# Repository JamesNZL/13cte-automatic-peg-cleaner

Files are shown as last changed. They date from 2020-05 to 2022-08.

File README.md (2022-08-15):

# Automatic Peg Cleaner

## Assessment Submissions

- [Brief Development `AS 91698`](./Documentation/Brief%20Development%20AS%2091698.pdf) (Achieved with Excellence)
- [Prototyping `AS 91611`](./Documentation/Prototyping%20AS%2091611.pdf) (Achieved with Excellence)
- [Electronics `AS 91904`](./Documentation/Electronics%20AS%2091904.pdf) (Achieved with Excellence)

## Issue

> Upon removal from the ground, my stakeholder’s tent pegs always have large amounts of soil and dirt stuck in between the three protruding beams.
> This is a common issue experienced with all tent pegs, but particularly Y stakes such as his, a Sea to Summit Ground Control Peg, but also similar products from other brands such as an MSR Groundhog.
> These pegs are very popular due to their high holding power and strength to weight ratio, with three beams to maximise the surface area of ground contact, and therefore the amount of friction.
> This also means that upon removal soil band dirt is likely to stick to the beams, particularly in softer ground with more moisture.

## Operating Principle

> Once a peg has been inserted through the hole in the top of the product, the laser tripwire is broken and the water jets automatically engage.
> Once the tripwire re-arms, the water jets disengage and the process repeats.
> If the laser tripwire is left intact for 3 minutes, the product will automatically turn itself off to conserve battery life.

## Conceptual Statement

> An intuitive, automated, eco-friendly solution to unreasonably dirty tent pegs of all shapes and sizes, this product easily cleans pegs to a brand new condition using high pressure water jets, automatically triggered by a laser tripwire.
> Economical in its water and energy consumption, all water used is also stored for recycling, and is easily used to water plants and flowers.

## Circuit Schematic

Circuit schematic

## PCB Design & 3D Render

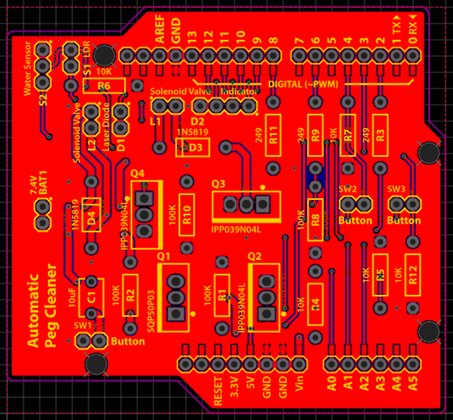
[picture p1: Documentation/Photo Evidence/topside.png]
PCB topside

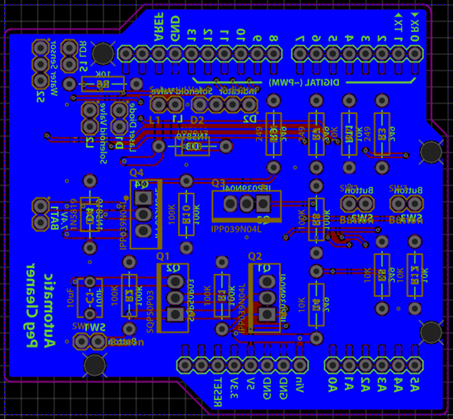
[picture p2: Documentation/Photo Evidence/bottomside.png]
PCB bottomside


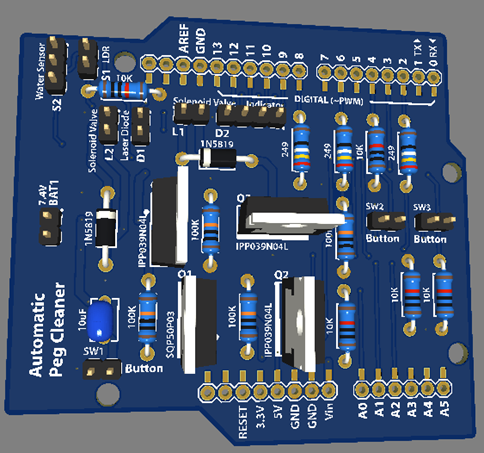
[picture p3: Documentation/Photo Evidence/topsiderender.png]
PCB topside render

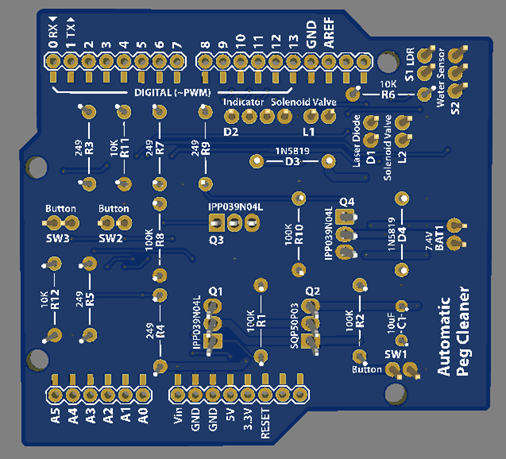
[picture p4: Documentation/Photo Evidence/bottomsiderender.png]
PCB bottomside render


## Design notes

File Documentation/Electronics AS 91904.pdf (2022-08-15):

jb16214 | Prototyping AS 91611 | 13CTE

# Electronics AS 91094

## Laser Tripwire

I started by hooking up an LDR to my Arduino and logging the analogRead() value, which returns the voltage between the output from the resistive divider created by the LDR and accompanying resistor
and ground. The circuit
at this stage looked like
as in Figure 1, with the
LDR in series with a 10k
resistor forming a
resistive voltage divider. To test this circuit, I ran the code as in Figure 2,
simply logging the
analogRead() from the
LDR pin.

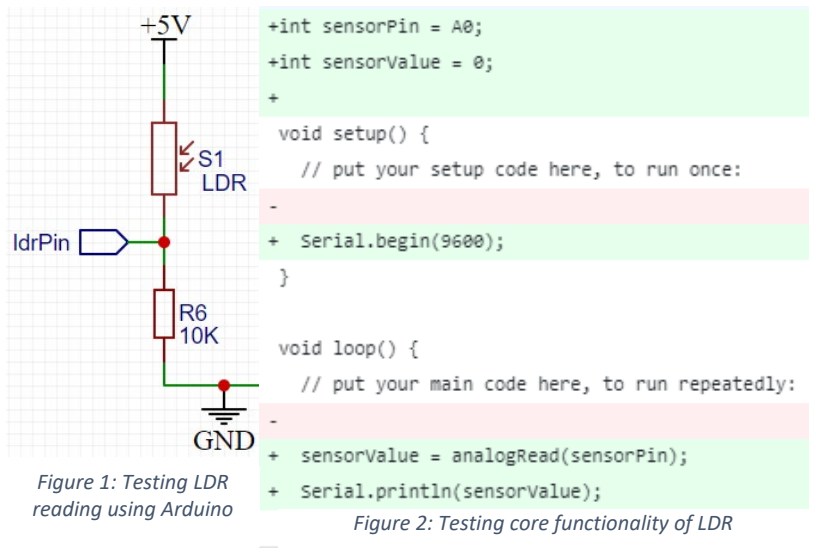
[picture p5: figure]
Figure 1: Testing LDR reading using Arduino

Once this behaved exactly as I was expecting, I added a trigger functionality to the code, with a variable defining a ‘trigger point’ where it would trigger if the light level was below triggerValue. I also made it so that the software would automatically calculate an appropriate light level to trigger at by reading the ambient light and finding the mid point between the ambient light level and the maximum possible reading, such that if the ambient light environment decreased it would trigger. By using this method in calculating the trigger point the code is far more versatile than if it were hard-coded in, as it could be moved from a brighter environment to a darker environment and still function as intended. This functions by trapping the code in a ‘while’ loop when the sensorValue is ‘safe’, only running the rest of the code when it falls below the trigger point. Although this is a bad solution for advanced programs as it is ‘blocking

Figure 2: Testing core functionality of LDR

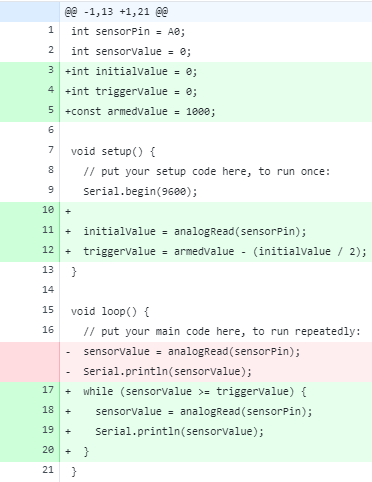
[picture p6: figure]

Figure 3: Implementing a trigger system code’, meaning no other code will run while the ‘while’ loop is still executing, it was sufficient for the proof-of-concept purposes I was using it for.
I ran into an issue with the code in Figure 3 as sensorValue was still set equal to 0 when it first ran the conditional statement of (sensorValue >= triggerValue), meaning it would immediately return false and therefore the while would never trigger. This meant that the tripwire would immediately trip, and the trigger system failed. To fix this, I initialised sensorValue = analogRead(sensorPin) before the while loop, to ensure it had a real value.

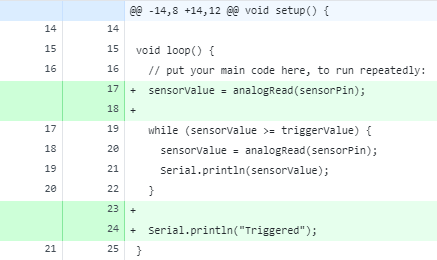
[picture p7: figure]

Figure 4: Bug fix for Figure 3
The next change I made was to improve the calculation for triggerValue, by increasing the data set used to calculate it by averaging out five values. This improves the accuracy of initialValue, and in turn results in a more accurate triggerValue.

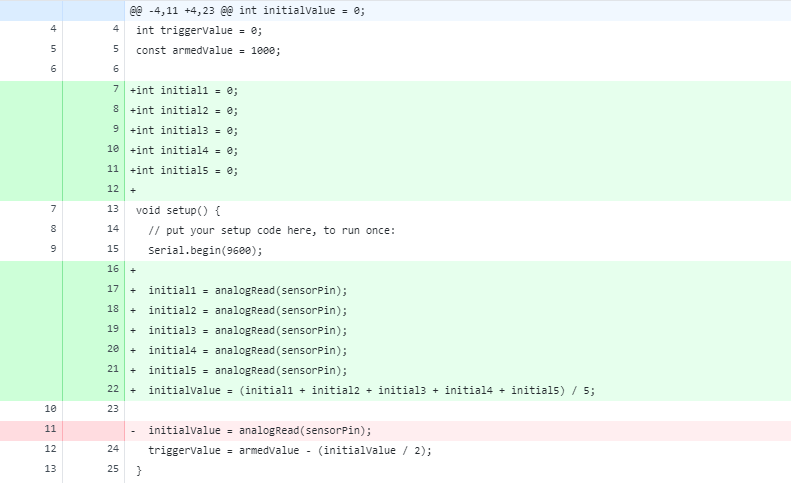
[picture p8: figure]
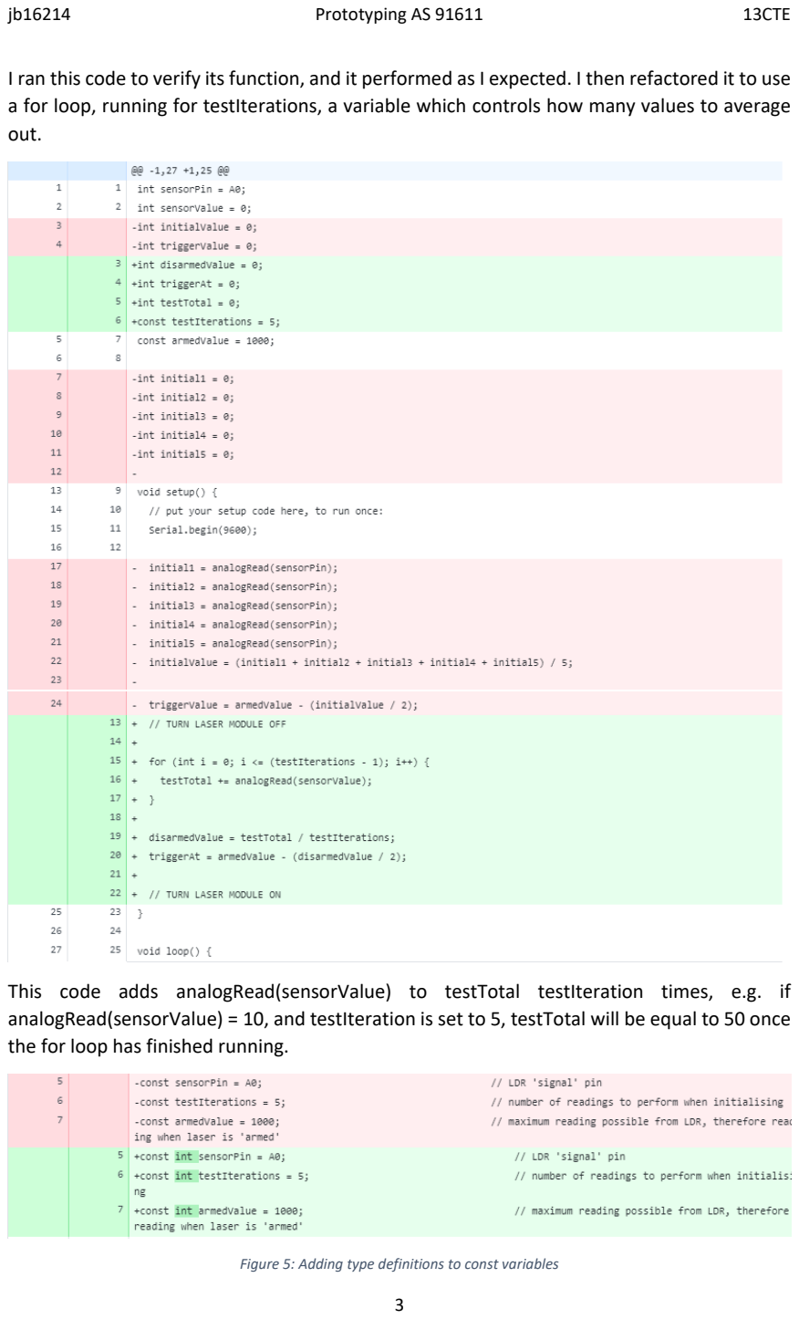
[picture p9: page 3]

I ran this code to verify its function, and it performed as I expected. I then refactored it to use a for loop, running for testIterations, a variable which controls how many values to average out.

This code adds analogRead(sensorValue) to testTotal testIteration times, e.g. if analogRead(sensorValue) = 10, and testIteration is set to 5, testTotal will be equal to 50 once the for loop has finished running.

Figure 5: Adding type definitions to const variables

## Laser Diode

Following some further minor optimisations to the LDR trigger code I then started on getting the laser to function, which I started with just setting up a Blink program with the laser connected to pin 13.

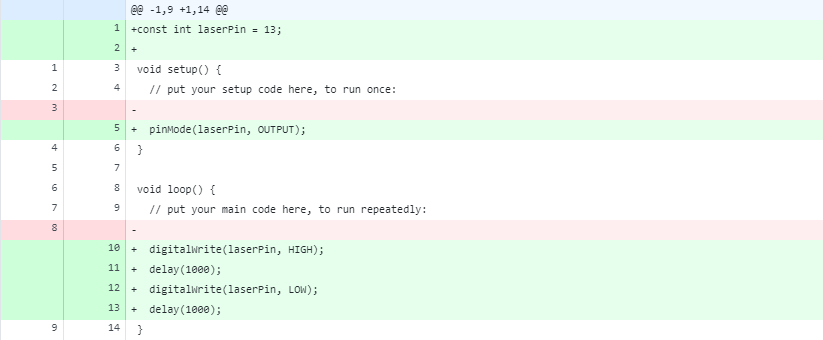
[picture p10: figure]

Once I verified through testing that the laser diode would behave exactly like a regular LED I then combined the two code files, adding the laser component of the tripwire system.

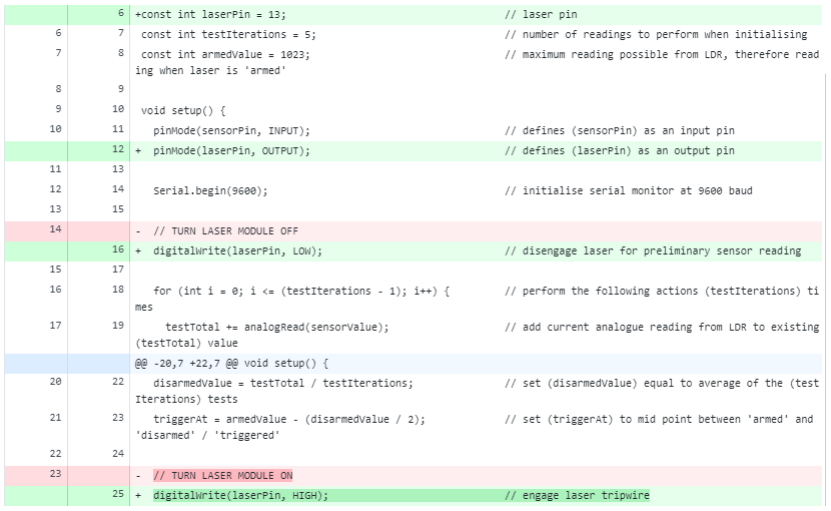
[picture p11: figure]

The first thing I did was to adjust the initialisation system to better represent the real trigger point, by ensuring the laser was turned off during the calculation. This means the real ambient value is taken, which can them be used to calculate an appropriate trigger value if the trigger value is broken and the laser is not in contact with the LDR. As the for loop is also ‘blocking code’, the laser will not be turned on until the readings have finished.

In order to test this code to ensure the calculation and tripwire is fully functioning, I added Serial.print lines to give debugging output, specifically logging the calculated value for triggerAt.

https://youtu.be/l-XJrVRsnDY - Testing laser tripwire

## RGB LED

Once I had my laser tripwire all testing and working, I then looked to add a red/green indicator to show whether everything was set up and good to go. To do this, I again created another proof-of-concept file, which I used to ensure the colour control would work as I was expecting it to.

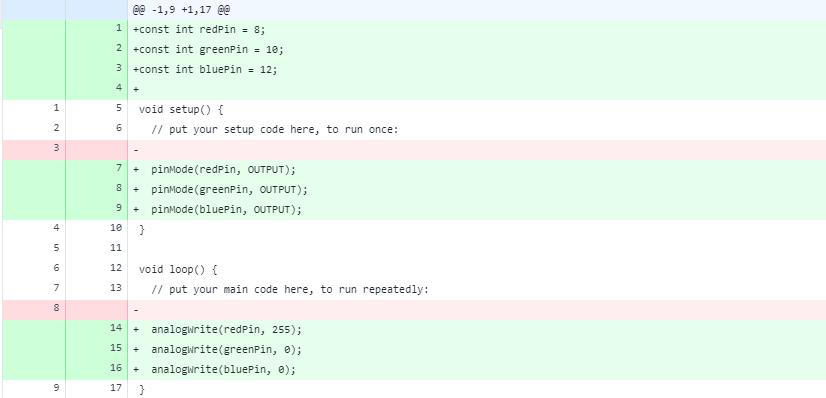
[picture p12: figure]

Once I ran and confirmed that this code functioned, I then decided to use digitalWrite() instead of analogWrite() for the RGB LEDs, as I did not need finer analog control, and I decided it would be easier to use a boolean set of 0/1 or LOW/HIGH instead of using 0 and 255.

I then implemented this RGB LED code into the main Laser Tripwire file, and configured it such that if the tripwire failed to initialise it would display red, or it would display green if everything were set up correctly.

https://youtu.be/d2IjNq5b3FE - Testing laser tripwire with RGB LED integration (LED is at bottom left of screen)

I then slightly refactored the laser tripwire code to do the ambient light level calculations before checking that the laser has turned on. This modifies the initialisation process from –
1. Turn laser on
2. Check laser is on
3. Turn laser off
4. Calculate ambient light level
5. Turn laser on
6. Check laser has turned on To –
1. Calculate ambient light level
2. Turn laser on
3. Check laser is on

I found that I had unexpected behaviour having the laser connected to pin 13 due to the Uno’s built in LED, and so I took the opportunity to re-map the pin assignments. I also used this chance to make sure the RGB LED pins were all next to each other, and so I decided to use pins 9, 10 and 11.

## Circuit Schematic

Once I had my proof of concept code files completed, I worked on developing the actual circuit for my project. To do this, I used EasyEDA to create my project schematic and later to produce the PCB design, the final results of which are shown below, with full development available alongside everything else in my GitHub repository: https://github.com/JamesNZL/13CTE, with development specific to the circuitry at: https://github.com/JamesNZL/13CTE/commits/master/Circuit/projects/Automatic%20Peg%20Cleaner. (https://github.com/JamesNZL/13CTE/commits/master/Circuit/projects/Automatic%20Peg%20Cleaner)
Commit history: https://github.com/JamesNZL/13CTE/commits/master

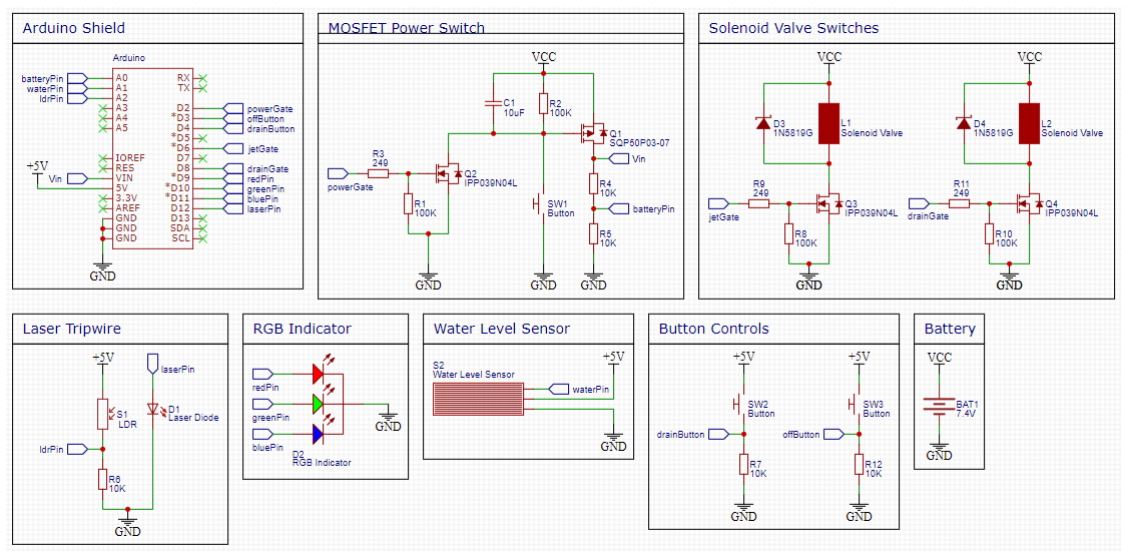
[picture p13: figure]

A notable design development choice I made was to add Schottky diodes D2 and D3 in reverse bias across the solenoid valves as flyback diodes, in order to prevent any unwanted voltage spikes and sparking due to the collapse of their magnetic fields.

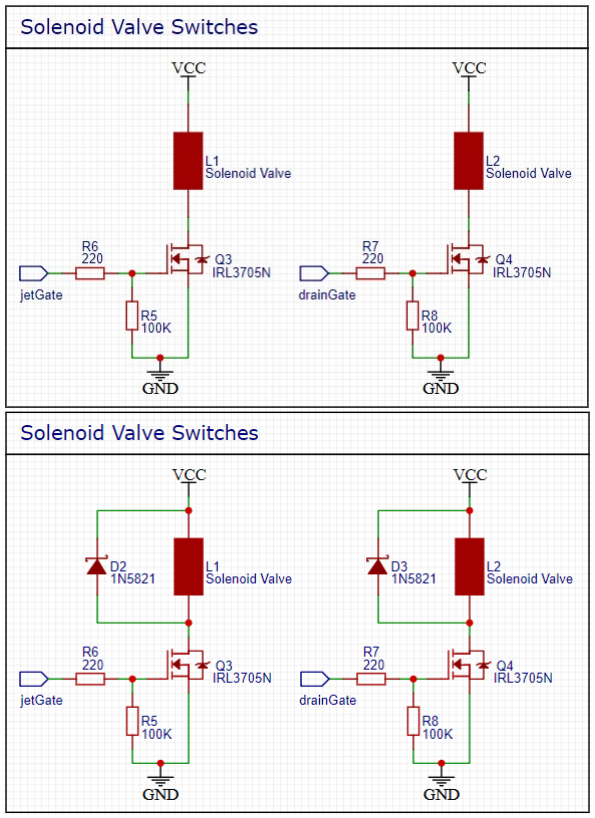
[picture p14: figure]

Another addition I made later on was the addition of a pair of voltage sense resistors R4 and R5 as shown in the image below, which form a resistive voltage divider allowing the Arduino to monitor the battery’s voltage. I used this to detect if the battery needed to be charged, notifying the user through blinking the indicator LED.

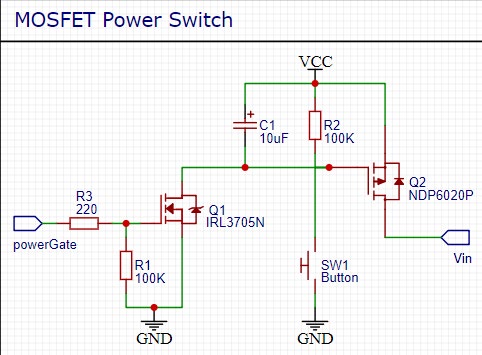
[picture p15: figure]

Figure 6: Without voltage sense resistors
Otherwise, my circuit schematic was reasonably straight-forward, with the only other circuit segment that was relatively advanced being the circuit for my MOSFET power switch, which I used to allow the Arduino to turn itself on when the user pushes the on button, and keeping itself on until the user pushes the off button.

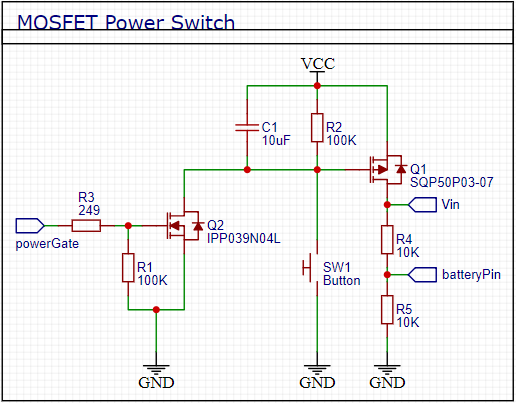
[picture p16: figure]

The way this circuit works is that the pair of P-Channel and N-Channel MOSFETs work together to switch the output of the circuit between GND and VCC, connected to the Arduino’s Vin pin, where the Arduino’s GND is permanently grounded. The circuit works as when the user pushes switch SW1 the gate of the P channel MOSFET Q1 is pulled to GND, connecting VCC at the drain to the Arduino’s Vin at the source. This means the Arduino begins to turn on, with a voltage output at batteryPin of half of the current voltage of the 7.4V nominal battery, which is used to check whether the battery needs to be recharged. SW1 can then be released as capacitor C1 will continue to keep the PMOS’s gate low, allowing the Arduino to fully boot. Once the Arduino has fully turned on, it outputs HIGH on the powerGate pin, keeping the NMOS Q2 switched in an ON state, which maintains the GND path for the gate of Q1. If the Arduino then needs to be turned off, it simply needs to switch powerGate LOW, which in turn switches Q1 off.

## Components Selection

I chose to use MOSFETs rather than NPN and PNP transistors for a variety of reasons, such as to minimise the current draw while switched on due to the tiny Rds(on) at 5V of just 0.0039 ohms and 0.007 ohms for my N and P MOS respectively. I found both using Digikey’s parametric search, from which the IPP039N04LGXKSA1 N-channel MOSFET and SQP50P03-07_GE3-ND P-channel MOSFET were the most appropriate for my needs and the most price effective in small quantities. Both MOSFETs are ‘logic level’, meaning they are designed for 3.3V or 5V logic circuits, with threshold voltages of gate-source (i.e. the voltage required to switch the MOSFET fully on) of 1.2V minimum and 2V maximum for the NMOS and -1.5V minimum and -2.5V maximum for the PMOS, easily manageable by my 7.4V battery / 5V Arduino.
I chose to place a gate resistor (R3) on my NMOS connected to the Arduino to ensure that the gate capacitance did not result in a high initial current draw greater than my Arduino can handle, therefore using Ohm’s law I used a maximum current draw of 20mA (half of the Arduino’s maximum of 40mA), which at 5V gives a resistance of 250 ohms, and so I chose a 249 ohm resistor. As MOSFETs are driven by voltage and not current (compared to a BJT transistor), there is no effect whatsoever on the speed or effectiveness of the FETs as switches. To calculate the power, I used PP = VV2
RR

with VV = 5 and RR = 250, giving me a

maximum instantaneous power draw of 0.1W. I decided to use a 1/4W resistor to give some buffer over the 0.0125W tolerance for a 1/8W resistor, with next-to-nil compromise in price or size.
I am also using gate pull down and pull up resistors (R1 and R2), to prevent floating states when the Arduino is turned off or when the switch and Arduino is off respectively for the N and P channel FETs, for which I chose 100K resistors to minimise the voltage loss over the resistive divider created by R1 and R3, and to minimise current draw to a miniscule 50 microamps, which is desirable for my battery-powered project.

To calculate the appropriate capacitance of C1 to sustain a reasonable boot time for the

# Arduino I used VV = VVss ⋅ ee

−tt
RRRR where V is equal to the threshold voltage of the FET’s gate, Vs is

the supply voltage (i.e. 7.4V), R is the resistor through which C is discharging, C being the capacitance value, and t being the time taken to discharge from Vs to V.
Rearranging for C, I got CC = −tt

# RRRRRR vv

vvss

# , into which I plugged in tt = 2, VV = −1, VVss = −7.4VV, RR = 100KK

to get C = 9.9926 E⁻⁶ Farads, or 10 microfarads.
By using 2 seconds I am ensuring that even with an extremely quick button press the Arduino will have enough time to fully turn on, which I am further ensuring by programming my Arduino using a second Arduino as ISP, meaning the Arduino does not need to run the bootloader and therefore is ready to go within milliseconds.
I did not require a current limiting resistor in series with my laser diode in order to protect my Arduino as it has an integrated 91 ohm resistor, which at its rated 5mW at 5V it will consume a maximum of 1mA, easily within the Arduino’s 40mA limit.
I determined an appropriate resistance to use in series with my LDR to create its voltage divider experimentally, using the following table:

I started by measuring the resistance of the LDR at varying light levels using a digital multimeter, and then using a 10k resistor and a 47k resistor and trying the results. I chose the values of 10k and 47k in an attempt to concentrate the accuracy of the LDR in the range where the ambient lighting will typically be, i.e. in an enclosed 3D printed product. Therefore, I chose 10k to create a 50/50 ratio at a dim light level and 47k to experiment tending towards a darker environment, as 47k was the closest value I had to 50k. Even accounting for the expected darker light levels of the final product, I found it was overwhelmingly more reliable to stick with a 10k resistor for maximum versatility, and therefore I did so.
For the armed tripwire, a maximum voltage of 4.943V translates to an analog reading of 1011, as 0.9889 (voltage divider ratio) * 1023 (maximum value) = 1011.

I decided it was not necessary to include reverse polarity protection in my circuitry, as I am using a keyed XT60 connector for my LiPo battery and a keyed MOLEX connector to connect my peg cleaner to the control box, therefore there is next to no risk of reverse polarity in normal operation.
To decide on a flyback diode for my solenoid valves I was looking for an average forward current of around 1A, to provide a decent buffer for the 500mA of current draw I expected from my solenoid valves. Using the DigiKey parametric search, I found the 1N5819, which has up to 25A of surge current and up to 40V of reverse voltage, meaning it was more than adequate for my application.

## PCB Development

My initial plan to produce and fabricate my PCB was to use our previous Voltera prototyping machine to validate that the circuit was fully functional on a proper board and not just on the breadboard, after which I would have it fabricated by a prototyping company such as JLCPCB. Multiple aspects of the plan changed however, and I ended up not having the time to realistically send my completed PCB design off and wait for it to arrive, and also we moved away from the Voltera printed ink circuit boards back to a CNC miller. Therefore, my final PCB being used in my project was produced using the school’s CNC miller.
Various different versions of my PCB design:

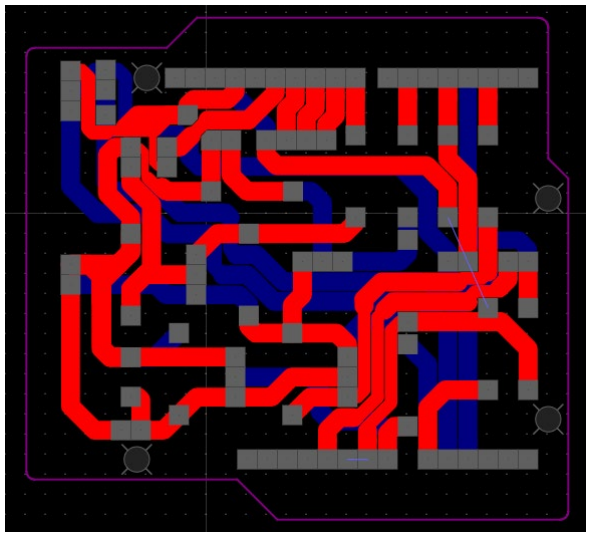
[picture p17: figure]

Figure 7: Top layer of my EasyEDA PCB design for the miller

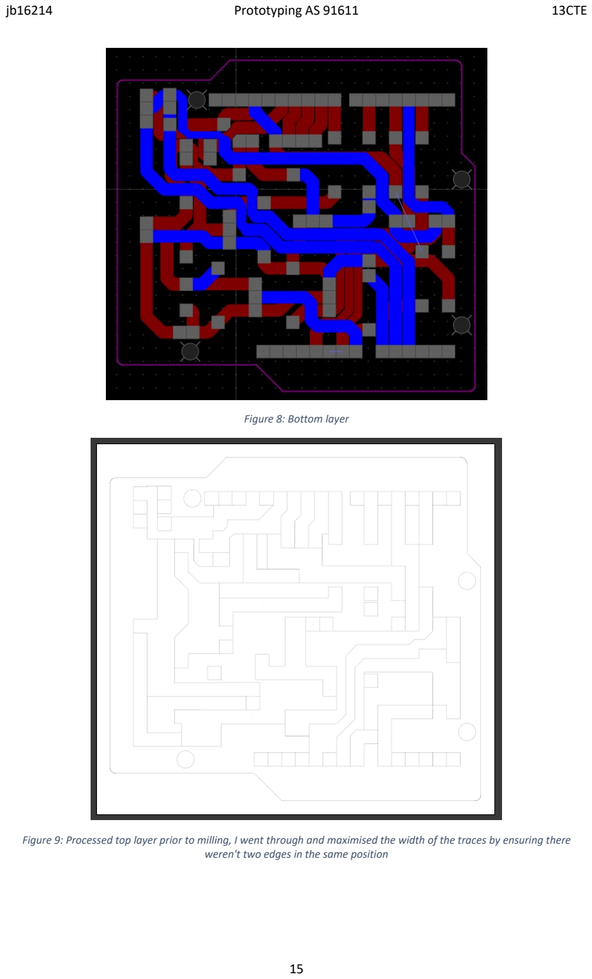
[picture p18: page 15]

Figure 8: Bottom layer

Figure 9: Processed top layer prior to milling, I went through and maximised the width of the traces by ensuring there weren't two edges in the same position

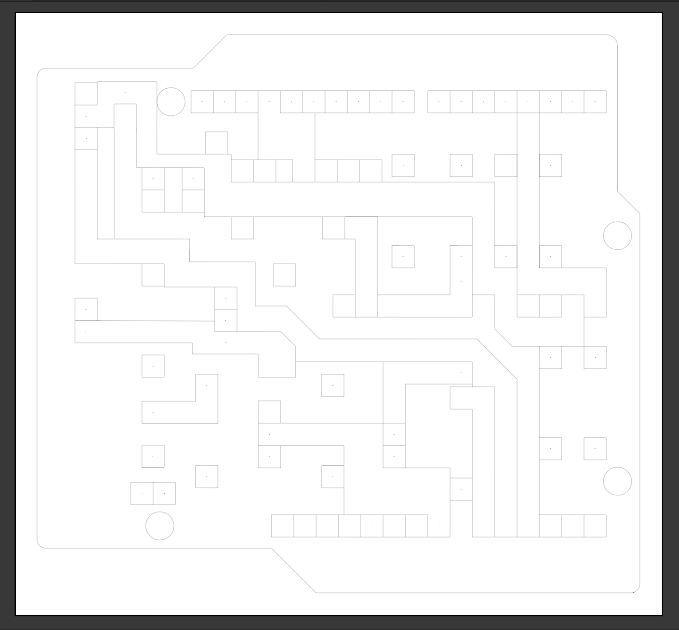
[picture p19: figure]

Figure 10: Processed bottom layer

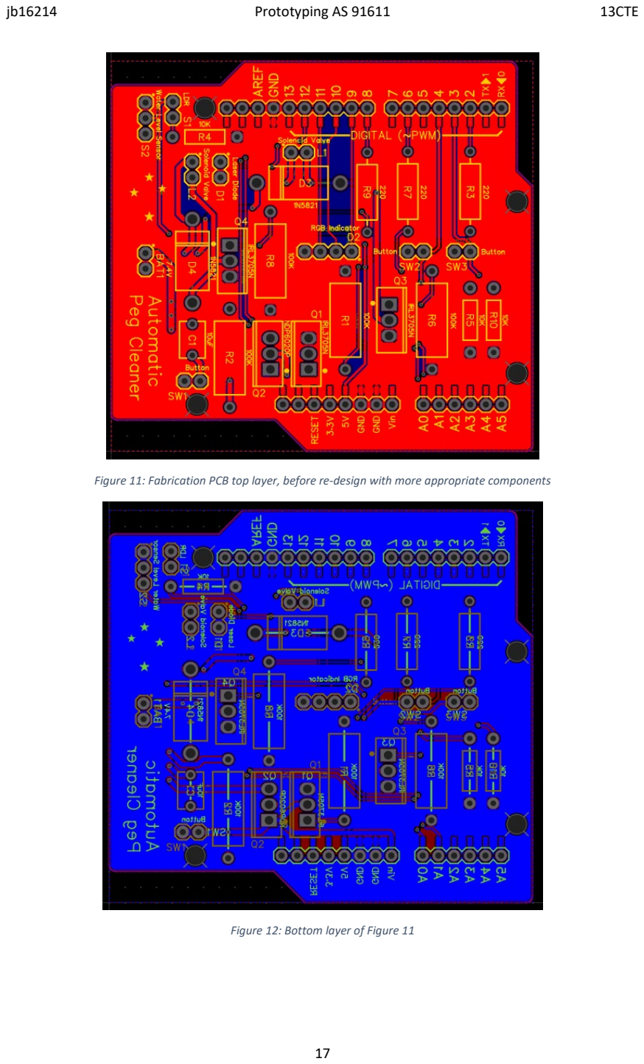
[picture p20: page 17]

Figure 11: Fabrication PCB top layer, before re-design with more appropriate components

Figure 12: Bottom layer of Figure 11

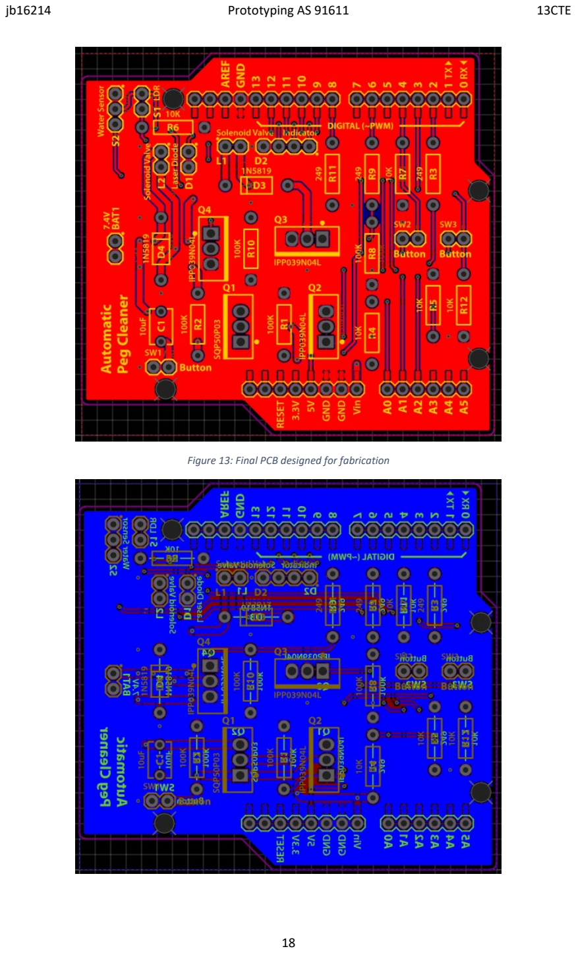
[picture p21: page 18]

Figure 13: Final PCB designed for fabrication

For my early versions such as the one I designed for the Voltera, my only goal was to ensure good quality electrical connections between A and B, in order to verify the performance and functionality of the circuit. Once I achieved that, I then went back and continued to iterate and improve, using design best practises such as using a GND plane/copper fill on my boards, enforcing a convention of North-South and East-West on my top/bottom layers to avoid routing conflicts, using vias to tidy up board layouts, and using GND stitching vias. By aiming to have my designs fabricated professionally, I was able to incorporate these elements into my designs as I could be confident that they would be able to be produced within the capabilities of the machines, unlike if I were to make them myself.
As we eventually moved away from using the Voltera at school, it meant the capabilities and restrictions I had to prototype my board at school changed drastically, as the CNC miller offered some significant advantages but also some disadvantages over the Voltera. The miller is far more robust and easier to operate than the Voltera, resulting in a board that is easier to debug and test, as well as to solder to. However, the design process to actually fabricate the board became far more complex, where while the Voltera simply needed the exported Gerber files directly from the PCB design software, the CamCut CNC required a proprietary and non-standardised .FAB fabrication file. This meant I had to export my designs from EasyEDA as a PDF rather than as a set of Gerber files, such that I could end up with a file readable by 2D Design. The only way we knew to get a workable .FAB file for the CNC miller was to export from 2D Design using a pre-loaded export engine and then run an executable on one of the school’s computers, and so I kept jumping through applications and file formats until I found one that resulted in a workable work-around. Eventually, I found I needed to export as a PDF and use Adobe Illustrator to convert it to a .DWG file readable by AutoCAD, which could then export as a .PLOT file that was recognisable by 2D design. We could then export using the CamCut PLOT settings, and putting that through the convert.exe, we ended up with a file that could be milled.
This meant it was somewhat more difficult to quickly prototype iterations of my PCB and especially if I wanted to use Illustrator to process my exported EasyEDA pdf so that the lines were as efficient as possible, however in the end resulted in a functional and working PCB.

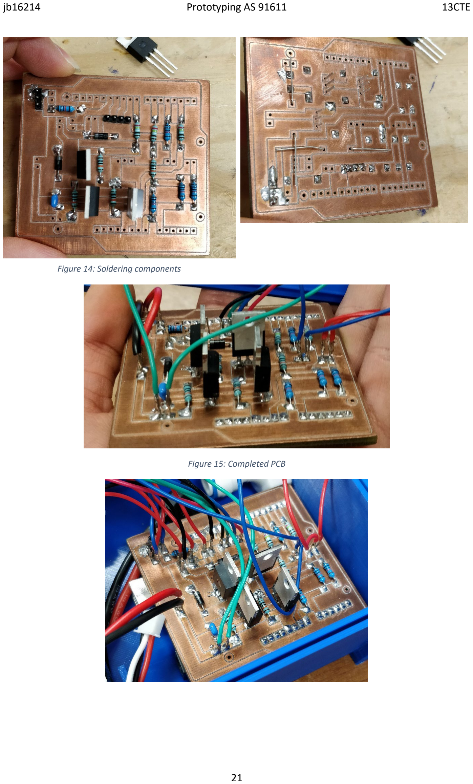
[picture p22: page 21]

Figure 15: Completed PCB

Figure 14: Soldering components

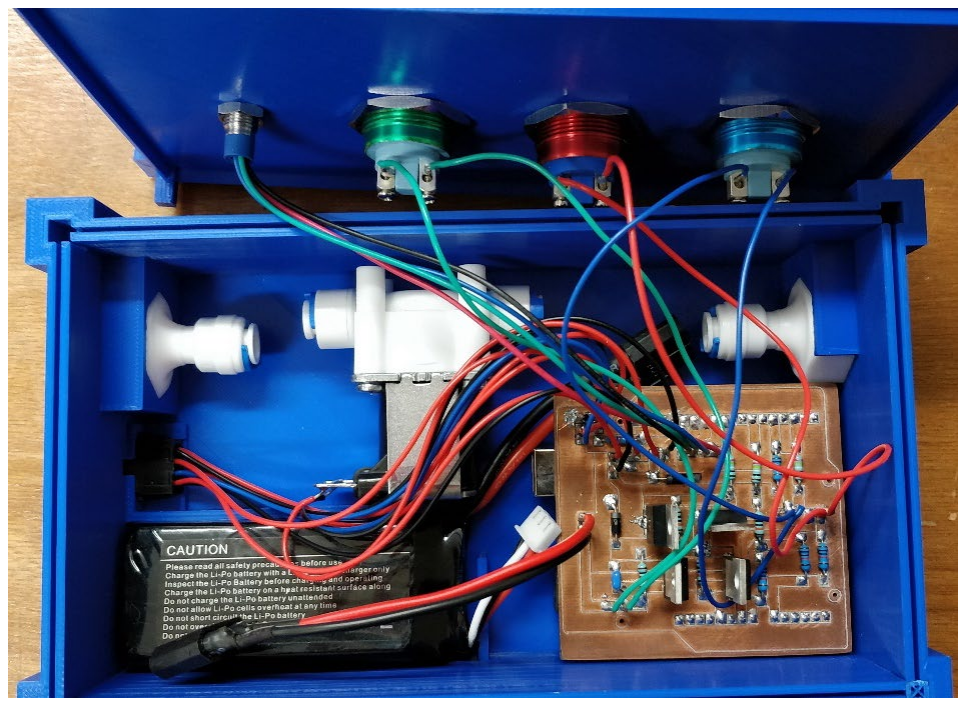
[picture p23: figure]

Figure 16: Completed PCB in enclosure

## Arduino as ISP

To program my Arduino, I used a second Arduino as a Programmer and used the ArduinoAsISP functionality to program the one I was using in my project. By using this method, I am ensuring the Arduino bootloader is not loaded on to my target Arduino, as therefore does not execute the bootloader processes when it first starts up. This consequently means that on start-up it immediately begins running my project code, and therefore will switch the pin connected to the MOSFET on extremely quickly. I decided to use this method of programming my target Arduino instead of the usual direct upload as by using the conventional upload, the IDE will automatically also upload Arduino’s bootloader to the target alongside the project code, which runs on start-up. What the bootloader does is check if the Arduino is trying to be programmed, and if so establishesthe connection in order to accept the incoming code. Although this only takes roughly a second to fully complete and to move on to the actual project code, I needed the target to turn on as

quickly as possible in order to ensure the capacitor did not discharge below the threshold needed to have the Arduino turn on, in the event that the user only gave the button a short tap.
Arduino as ISP uploads the program code from the programmer to the target using the SPI interface/protocol, or Serial Peripheral Interface. SPI is a synchronous interface, meaning that there is a clock signal controlled by the master device, i.e. the programmer, and used by the

Figure 17: From
https://www.arduino.cc/en/Tutorial/BuiltInExamples/ArduinoISP (https://www.arduino.cc/en/Tutorial/BuiltInExamples/ArduinoISP)

slave device(s), i.e. the target. SPI uses four pins as shown in the diagram above (not including the +5V and GND connections), by convention called SCLK, MOSI, MISO and SS.
SCLK | Serial clock | Controlled/output by the master device for synchronising the serial communication
MOSI | Master Out Slave In | Communication line from master to slave
MISO | Master In Slave Out | Communication line from slave to master
SS | Slave select | Controlled by master to select the target slave device

On the Arduino Uno, these are both stand-alone on the edge of board as in the Figure below, however they are also accessible through the digital pins 10-13, for SS, MOSI, MISO and SCLK

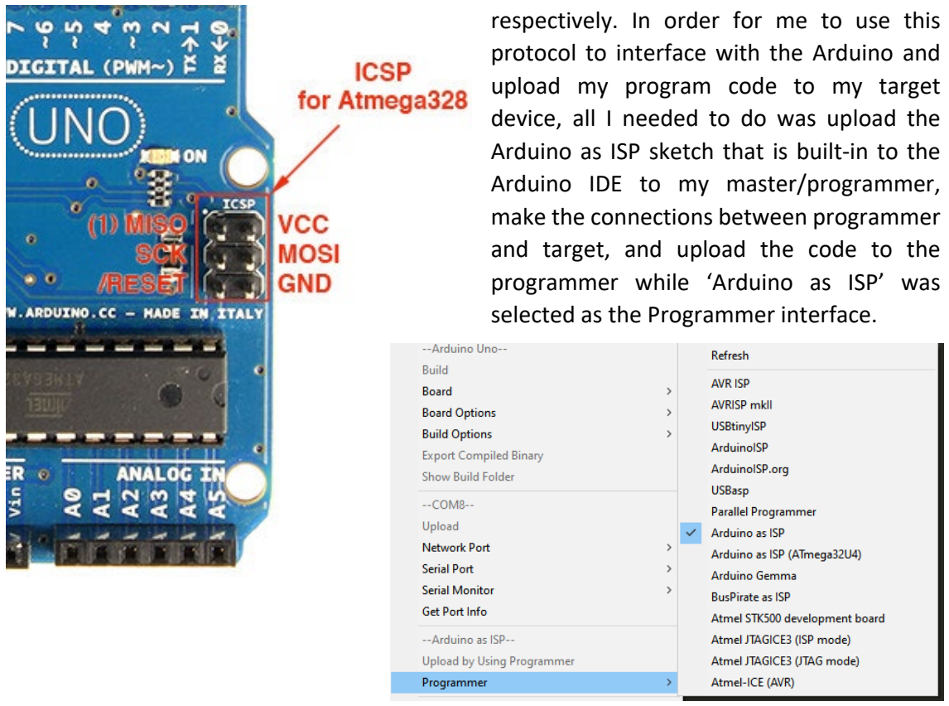
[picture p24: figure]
upload my program code to my target; Arduino IDE to my master/programmer, make the connections between programmer and target, and upload the code to the programmer while ‘Arduino as ISP’ was selected as the Programmer interface.

respectively. In order for me to use this protocol to interface with the Arduino and

device, all I needed to do was upload the Arduino as ISP sketch that is built-in to the

For the rest of my project, I did not need to use any other communication protocols as my subsystem was wired directly to my PCB using a connector and did not have any active components that needed to be communicated with, as all the MOSFET switching circuits were controlled on my PCB. If I were to re-make this project, I would look more in depth into creating a wireless control module for the sub-system, and communicating over Bluetooth or another wireless interface, so that I do not need to have wires connecting the PCB to the actual peg cleaner.

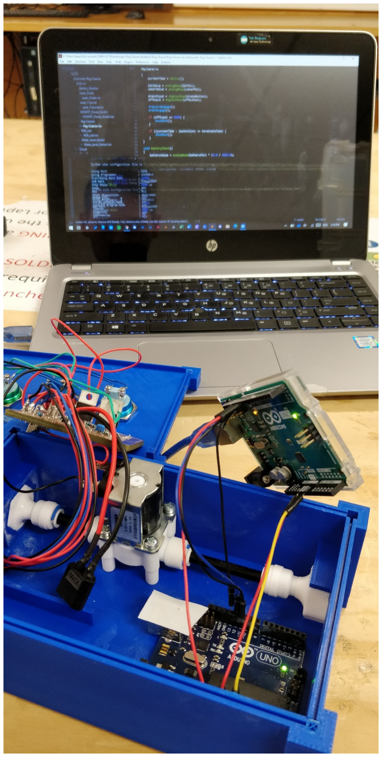
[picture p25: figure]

Figure 18: Uploading using Arduino as ISP

## Appendix of Evidence

https://youtu.be/9pyqVOlHjWM - Testing using a single NMOS for the switching circuit, does not work as Arduino turns on even before button is pressed
https://youtu.be/B2iy4qF7UdA - Switching circuit with relay, functions perfectly however relay was not suitable for final product due to power consumption and physical size https://youtu.be/7_AMME0NAls - Testing analogRead values with water level sensor https://youtu.be/zFWam2sqd8s - Testing accuracy of the defined water danger value https://youtu.be/cPWKj5jhYVU - Changed minimum value as a result of testing https://youtu.be/0_3hpAmIIrM - Testing the MOSFET switching circuit, Arduino programmed conventionally
https://youtu.be/LsTzG-rKk8Q - Testing MOSFET switching circuit with target Arduino programmed with Arduino as ISP
https://youtu.be/iif9ogpAt94 - Testing turning off indicator LED after capacitor discharges, i.e. when Arduino fully shuts down (feels laggy)
https://youtu.be/blNLxr6ts74 - Testing turning off indicator LED before capacitor discharges, i.e. before Arduino fully shuts down (feels responsive, however not fully accurate to Arduino being off)
https://youtu.be/aM0B3x9BfSc - Testing indicator LED colour conditions to ensure it is fully functional

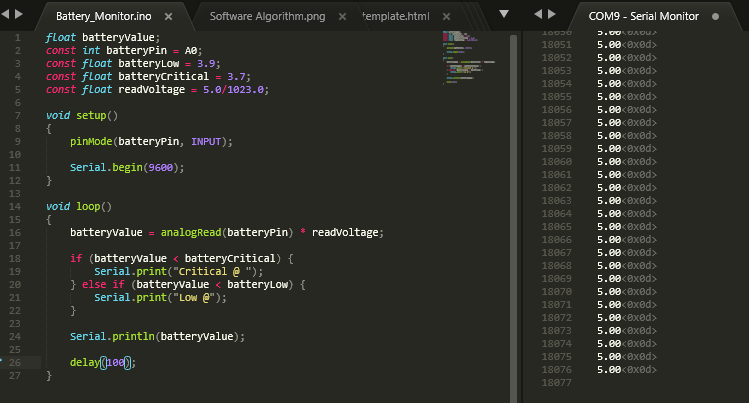
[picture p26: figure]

Figure 19: Testing battery monitoring circuit

I tested the battery monitoring voltage divider by using the Arduino’s 5V and 3.3V pins, and 20k/6.8k ohm voltage divider to test supplying pin A0 with differing voltage levels, and testing the processing/output value.

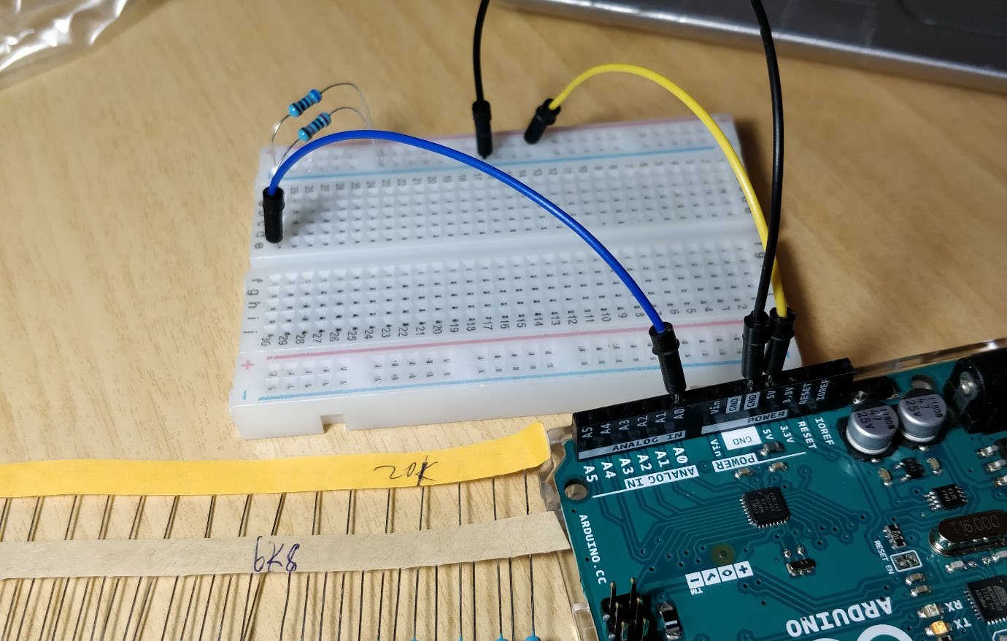
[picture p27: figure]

## Final Code Development

Final version -
https://github.com/JamesNZL/13CTE/blob/master/Arduino/Peg%20Cleaner/Peg%20Cleaner .ino (https://github.com/JamesNZL/13CTE/blob/master/Arduino/Peg%20Cleaner/Peg%20Cleaner.ino)
I started off duplicating my most recent copy of Laser_Tripwire.ino, which was a finished copy of the laser tripwire module with indictor LED integration, and now I needed to add the control for the solenoids, Arduino, and water level sensor, and make sure they all work alongside each other.
First I adapted my variable names and pin numbers into my final configuration as per my schematic, and then I added code to have the water level sensor turn the drain on and turn the LED red if it was above the danger level.

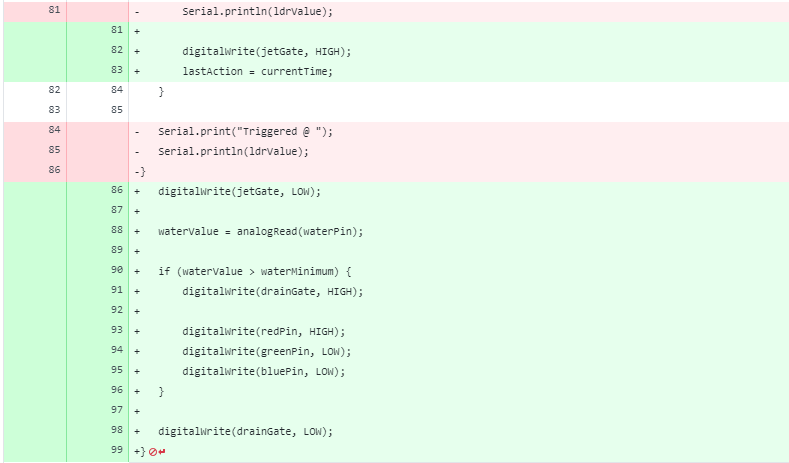
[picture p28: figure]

The next significant change I made was to move from the ‘blocking’ while loops towards if statements, which would allow other code to run alongside.

Some more changes and fixes I made include adding the time out functionality:

Which I had to fix as lastAction would go over terminateTime almost immediately, and so I needed to find the difference between the current time and the last action:

I then began to refactor code into functions so that it was not all in one massive loop() function, instead the loop
() simply calls the sub-modules:

I needed to fix the battery voltage reading by actually converting it to a voltage:

My laser tripwire statement was backwards, meaning it would turn the jets on etc. if the laser was NOT blocked:

I also added a ‘fluctuation trigger’, which if the LDR value changed outside of a tolerance while collecting testTotal, i.e. if it was reading an ambient light value of 100 then suddenly became 300, the fluctuation check would ensure the test is cancelled and restarted.

Figure 20: Adding break statement so calculation reset

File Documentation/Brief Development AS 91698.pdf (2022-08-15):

jb16214 | Brief Development AS 91608 | 13CTE


1

# Brief Development AS 91608


# Issue

Upon removal from the ground, my stakeholder’s tent pegs always have large amounts of soil and dirt stuck in between the three protruding beams, as shown in the image to the right. This is a common issue experienced with all tent pegs, but particularly Y stakes such as his, a Sea to Summit Ground Control Peg, but also similar products from other brands such as an MSR Groundhog. These pegs are very popular due to their high holding power and strength to weight ratio, with three beams to maximise the surface area of ground contact, and therefore the amount of friction. This also means that upon removal soil band dirt is likely to stick to the beams, particularly in softer ground with more moisture.


Figure 4: A peg puller with integrated brush | Figure 3: Shape of a 'Y' stake/peg
Figure 2: Example of left over debris | Figure 1: A Sea to Summit Ground Control peg

2

Some existing products that address this issue primarily involve brushes which are used to scrub the dirt and debris off, however these are typically ineffective for muddy soil that has dried onto the peg, or for soil that is stuck in the centre between the beams. Examples of these products include an item by Outdoor Revolution, which is a peg puller that includes a circular hole in the handle with brushes facing inwards. The peg is then inserted, in theory removing the debris.
As discussed above, these are typically ineffective for stakes of Y and other shapes, and are designed for use with traditional ‘shepherd’s hook’ stakes which are less likely to collect dirt, and typically simply have a layer of dust and similar light debris, which is easily brushed away. They are also typically awkward to use, as it requires holding both objects in your hands, and it is likely for the peg puller to rotate in your hand as you are unable to hold the grip while cleaning a peg, therefore needing to hold onto the cylindrical puller end.

# Stakeholder Consultation

## Primary Stakeholder – Bruno Prijic

### 1. Do you have any ideas to address your issue?

I have been thinking about things such as electric toothbrushes, but maybe improved to be more effective as I find that the toothbrush is too weak to displace all the dirt. I have also thought of using some sort of water gun.

### 2. What obstacles do you think may need to be considered?

I think if the water gun idea is going to be used then it needs to be carefully made, at least if it uses some sort of electronics. I think it would be hard to clean the pegs completely without using water, especially once the dirt has dried.

### 3. Have you seen any existing products that you might be interested in?

I have seen existing products such as the peg puller cleaner but I don’t think it would be very useful, so I think adapting things such as an electric toothbrush or a dishwasher on a small scale would likely be the best ideas.

3

# Ideas

In order to address this issue, I have considered a system similar to that of the existing brush-centred designs, though adapting and improving its function by implementing a motorised brush. This would reduce the manual exertion to operate the product, and would help with the ergonomics of the system. Another idea I considered was a water-based system that uses jets of water to blast away debris, potentially with a water collection system to conserve water, promoting sustainability. A third concept I have considered to address my issue is a simple scraper that is designed to specially fit around my tent pegs, in theory allowing the peg itself to pass through the cut out, but removing any debris attached.

## Concept 1: Motorised brush system

This concept would function similarly to an electric toothbrush, with a handle connected to a motor at the end connected to a brush head. It would feature an on-off or similar mechanism to turn the product on and off, and would likely need to be powered by a wall socket or a larger, bulkier battery.


## Concept 2: Scraper system

This concept involves a simple precision produced disk that has a hole perfectly sized to only let the size of a clean peg through, in theory scraping away any attached debris. It functions by simply inserting the tip end of the peg and sliding the product down, taking away all additional material attached to the peg.

Figure 5: Conceptual diagram of the motorised brush


Figure 7: Side view Figure 6: Top view


4

## Concept 3: Water blaster system

This concept involves a containment system to prevent water from escaping, with an entry hole in the top of the box. There would be a laser detection system in the top of the container to detect when a peg has been inserted, automatically turning on the water jets. There would be a water level sensor at the side to detect once the water level inside the container has reached an ‘emergency’ level, automatically opening the drain at the bottom, until the water is below the sensor. Otherwise, the drain remains normally closed until the user actuates a button, which allows for the water to be reused for something such as watering plants.

# Stakeholder Feedback

## Primary Stakeholder – Bruno Prijic

### 1. What are your thoughts on the three concepts?

I like the concepts and think they all have good potential to fix my problem, and I like the look of their features.

### 2. Which concept do you think will most successfully address your issue?

Personally I think that concept 3 will be most effective, as I think it would be the one that is most likely to completely clean my pegs, meaning I don’t need to do anything after using the product other than let them dry.

### 3. Is there anything which you think should be adjusted for that concept?

I would like it if it could also accept a variety of pegs of different shapes and sizes, in case I change pegs in the future or someone else needs to use the product.

Figure 9: Side view | Figure 8: Top view

5

# Decision Making

Concept | Positives | Negatives
Motorised Brush | This concept would build upon the effectiveness of existing products, and only requires easy to find parts. It would likely be effective with all types of debris, though may require patience depending on the type of debris and the strength of the motor. | It may end up being similarly awkward to the existing products in an ergonomics sense, having to hold a peg while controlling the motorised brush. It may also require enhanced ingress protection if using water to remove some debris prior to use, in order to avoid water damage to the circuitry. It is unlikely a hobby motor will provide sufficient power, therefore is likely to require larger batteries or a power adapter to power the motor, reducing the mobility of the product.
Scraper | This concept would be the easiest to manufacture, as it simply requires a 3D printer or a laser cutter to produce a functional scraper. This concept is also the most lightweight and portable product, meaning it is most appropriate to pack as gear for usage in the field, instead of once the user has returned home. | Although easy to manufacture, this product would have to be made specifically for each model of peg for maximum effectiveness, to ensure a snug fit to prevent any debris from remaining behind. It is also unlikely to result in a completely clean peg, as a thin coat of dust and dried mud is likely to remain stuck, or the finish on the peg may be damaged. It is also the hardest product to use, as it would require either pressing the end of the peg against a hard surface or against your hand, which would be uncomfortable due to the sharp points.
Water Blaster | Given sufficient water pressure, it is likely that this product can easily take care of all types of debris with ease, and given the small footprint of the stake, without much water usage. With a collection system, the water used could be repurposed to water plants or other similar activities, without wasting water. This would also be the easiest system to use out of the three concepts, as the user simply needs to lower the peg into the system, without needing to exert effort. | Due to the usage of water, there is an inherent risk to the electronics, which must be considered to prevent damage. While water is conserved, it is still a consideration that must be made, as it would be inappropriate to use it in environments where water restrictions frequently occur.

After considering the positives and negatives of each concept, and consultation with the primary stakeholder, I have decided to proceed with concept 3, the water blaster system. We believe that this is likely to be the most effective system for ensuring a complete clean, with the fewest and least significant cons, as discussed in the table above.

6

# Ongoing Stakeholder Feedback

## Primary Stakeholder – Bruno Prijic

### 1. What is your role in this project?

I am the main stakeholder in this project.

### 2. Who is this product for?

This product is for me to address my issue.

### 3. When is the product required by?

This product is required by the end of the year, at the latest.

### 4. What worries you about this project? What’s the worst thing that could happen?

The worst thing that could happen with this project is that it fails to function, and damages itself or my pegs. The inclusion of water is something that I have concern about, which needs to be managed.

### 5. How will you, personally, define success for this project?

If this project succeeds in cleaning my pegs completely, without leaving anything behind.

### 6. How would you like to be involved in the rest of the project?

I would like to have regular status updates, and being kept up-to-date on issues and delays. I would also like to be contacted frequently about decisions on aesthetics and functionality, to ensure it works as I want it to.

### 7. What does the perfect solution have?

Solves my issue, looks good, easy to store.

### 8. What kind of functionality do you want the product to have?

I would like it if it was as automated as possible, so it would be good if it could detect when I insert a dirty peg and then cleans it automatically.

7

### 9. What kind of aesthetic do you want the product to have?

I don’t mind, but I want it to look professional and tidy.

### 10. What is the ideal size for the product?

I want it to be no bigger than the rough dimensions of a milk bottle, but would be good if it was as compact and storable as possible.

### 11. What overall shape are you after for the product?

I don’t mind too much, whichever minimises the footprint of the final design.

### 12. What material do you want the product to be made from?

Ideally plastic to save weight and cost, like 3D printed or something similar.

### 13. What colour finish do you want the product to have?

Blue, grey or black would be nice, though it’s not a big deal.

## Secondary Stakeholder – Lucija Prijic

### 1. What is your role in this project?

I am the mother of the primary stakeholder.

### 2. Who is this product for?

This product is for my son.

### 3. What worries you about this project? What’s the worst thing that could happen?

For me, I am concerned about the water consumption of the product, and for me the worst thing that could happen is that there is a big impact on our household water usage and on the environment.

### 4. How will you, personally, define success for this project?

I would say that this project is successful if is uses as little water as it can, or it stores all the water to be reused.

8

### 5. How would you like to be involved in the rest of the project?

I don’t mind about regular updates; however I would like to be contacted with new updates around the consumption of water.

### 6. What kind of functionality do you want the product to have?

I would like if it could store the used water so I can use it to water my garden or my flowers.

### 7. What is the ideal size for the product?

I think a good size will be around the size of this plant pot [16 cm in diameter], which would be small enough for me to easily keep it somewhere around the house.

## Secondary Stakeholder – Moe Prijic

### 1. What is your role in this project?

My son is the main stakeholder.

### 2. Who is this product for?

My son.

### 3. What worries you about this project? What’s the worst thing that could happen?

I am interested about how much power it will require, so I would like if it was very energy efficient.

### 4. How will you, personally, define success for this project?

Small, low power and water consumption.

### 5. How would you like to be involved in the rest of the project?

I would like to be informed when the power method and water consumption is decided and if/when it is updated.

### 6. What kind of functionality do you want the product to have?

It would be good if it could have a way to turn itself off as sometimes my son is not very good at turning things off.

# Location Research


9

### 7. What is the ideal size for the product?

I would like if it was no bigger than my coffee tin, which is around 18cm x 22cm.


10

The primary physical environment this product will be used in is outside the stakeholder’s house, where the garden and outdoor hose are located. This ensures that unintentional water leakage will not be a concern when connecting and disconnecting the product, and means that recycling the used water in the product is as streamlined as possible. The concrete ground in the location is not perfectly flat, and therefore the product will require a stable base to ensure it does not tip over while in operation. As the ground is concrete, it would be ideal for the product to have feet made out of rubber or a similar material to prevent damage, reduce slippage, and limit vibrations while being used. The hose head is removeable and connects to the hose with a standard 12mm fitting, and so it would be preferable if the product could attach to the hose with its own 12mm fitting, preferably removable to widen the product’s possible use cases. While possible to lower an extension lead from the kitchen window located above the garden hose or from his dad’s workshop in the crawlspace underneath the house, it would be ideal for simplicity and overall functionality for the product to be battery powered.


11

# Implications and Considerations

Following consultation from my primary stakeholder and the secondary stakeholders who will also be impacted by the outcome, I have recognised the need to ensure my product is compact and storable, efficient in its water and power consumption, effective in addressing my stakeholder’s issue, suited to its environment, and adaptable for a variety of locations. For my stakeholder, it is imperative that the product fully addresses his issue and completely cleans his pegs, and has a tidy aesthetic design. For him, it is also desirable that the product is as automated as possible, detecting when he inserts a peg and automatically engaging the jets. The biggest impact of the product for his mother is the water consumption, even more important now due to Auckland’s dry spell and the trend towards drier summers. She would like for it to use as little water as possible, or at the minimum for the outcome to retain the used water to be recycled for purposes such as watering her plants and flowers. My primary stakeholder’s dad is particularly focussed on the power consumption alongside the water usage, as according to him my stakeholder is not the best at turning things off. Therefore, he would like for the product to automatically turn itself off after being idled for an extended period of time. A factor shared by all three stakeholders is the importance of storability, all preferring a compact product which is no larger than the rough dimensions of a milk bottle.

# Chosen Outcome

The outcome I have decided to pursue is concept 3, the water blaster system. Following initial consultation and ongoing feedback from my primary stakeholder and the secondary stakeholders, I have adapted the initial functions detailed at the conceptual phase into the following functions to best suit the needs of everyone who will be impacted by the product. The product will be battery powered and connect to the garden hose using a removable 12mm garden fitting, with a containment system to collect all the water used. The drainage system will be normally closed, and opened either by user input or if the water level rises above the emergency water level sensor. The drain will have sprinkler holes similar to a watering can, to suit recycling the water by using it to water plants. Once a peg has been inserted through the hole in the top of the product, the laser tripwire is broken and the water jets automatically engage. Once the tripwire re-arms, the water jets disengage and the process repeats. If the laser tripwire is left intact for 3 minutes, the product will automatically turn itself off to conserve battery life.

12

# Attributes

## Physical

Lightweight. The product should be made out of 3D printed plastic or a similar lightweight and cheap material, with the added benefit of being easily manipulated and adjusted.
Blue, grey or black. The product should be made out of or finished in a blue, grey or black colouring.
Professional. The product should be professional in appearance, with no messy wiring.
Robust and durable. The product should be made with quality in mind, to maximise the lifespan of the product.
Compact and storable. The product should be no larger than the rough dimensions of a 2L milk bottle to ensure storability and sleekness.

## Functional

Automated. The product should automatically detect once a peg has been inserted and begin the cleaning process. It should also automatically drain contained water if necessary, and automatically power off if left unattended.
Effective. The product should be capable of completely addressing the issue and cleaning all debris off the peg.
Versatile. The product should be adaptable for a variety of locations and water supply systems.
Stable. The product should feature a stable base with rubber or similar high-friction footing to maintain stability on sloped concrete.

## Social

Eco-friendly. The product should be economical in its water and power consumption, and should contain all water used to be repurposed. Intuitive. The product should be intuitive to use, with logical and user-friendly layouts and inputs.
User friendly. The product should be easily maintained, being easily connected to a water source and easily recharged.
Minimal set up. The product should not require any additional set up other than connecting a water source and ensuring the battery is charged.

13

# Conceptual Statement

An intuitive, automated, eco-friendly solution to unreasonably dirty tent pegs of all shapes and sizes, this product easily cleans pegs to a brand new condition using high pressure water jets, automatically triggered by a laser tripwire. Economical in its water and energy consumption, all water used is also stored for recycling, and is easily used to water plants and flowers.

# Specifications

The product will be constructed out of a lightweight, cheap but versatile material such as 3D printed plastic. This will ensure a cost effective product that is easily developed and iterated.
The product will be blue, grey or black in colour to fulfil my stakeholder’s requests. I will decide which colour to move forward with after researching the availability and feasibility of each, then seeing which will look the best.
The product will have a professional appearance and design, with no messy wiring. I will achieve this by ensuring all wiring and componentry is tidily laid out and hidden in enclosures.
The product will be robust and durable to maximise the lifespan of the product. This will be achieved through care during production and ensuring quality is always a priority.
The product will be no larger than 270mm x 180mm to ensure compactness and storability. This is derived from stakeholder consultation and feedback, where the directive has been that the product should be no larger than the rough dimensions of a 2L milk bottle.
The product will be portable, allowing the user to store it away inside their house and easily move it around. This will involve ensuring the product is lightweight and easily held.
The product will be watertight to contain all used water and to protect all electronic components and circuitry. To meet this specification, I will explore production methods such as using 3D printing or laser cutting sheets of acrylic and gluing them together to ensure complete ingress and egress protection. The product will be automated, requiring minimal user input. This will be achieved through a microcontroller such as an Arduino Uno, and electronic components and circuitry.

14

The product will have the capability to detect when a peg is inserted, automatically engaging the water jets. This is to be achieved by a laser tripwire system with a laser module and a photoresistor/LDR, to ensure maximum functionality in all conditions.
The product will have a system to turn itself on and off in order to conserve the longevity of the battery and reduce the frequency of recharging the battery. The product will successfully address my stakeholder’s issue by completely cleaning all dirt and mud off a Sea to Summit Ground Control tent peg. This is to be met through using some type of water jets to ensure no dried dirt or mud is left behind.
The product will be highly versatile to ensure it suits as many use cases as possible. This will be achieved by ensuring the opening at the top of the product is designed to suit as many shapes and sizes of peg as possible, while still preventing unwanted ingress of objects and egress of water while in operation. Further, the product will be designed to work with a variety of water source systems.
The product will be stable while in operation to ensure it does not tip over while in use. This must include a stable base with some type of rubber or similar footing to maintain stability on the sloped concrete at the location where the product is to be used and also to limit vibrations which may damage the product and make it more likely to tip.
The product will be environmentally friendly. This is to include minimal water and power consumption and recycling all consumed water through watering plants and other uses. This is to be optimised by ensuring the drain has small sprinkler holes to facilitate watering directly from the product.
The product will be economical in its water and power consumption. This will be achieved through ensuring an efficient use of water with high pressure but low volume water jets, and power efficient components that are automatically turned off if not in use.
The product will be intuitive and easy to use, with labelled and well-designed user inputs, to ensure a smooth user experience.
The product will be user friendly, with easily removed battery and water source connectors. This will be achieved using universal connectors and well-designed layouts that are intuitive and easy to operate.
The product will require minimal set-up and assembly to ensure a smooth user experience, with the user only needing to connect a charged battery and connect the product to a water source. This will be met by ensuring the product is fully functional prior to delivery through comprehensive testing.
The product will be easily maintained by the user, with easy access to the battery for a smooth recharging process. It should also offer easy access to electronic components and circuitry to allow for easy troubleshooting.
The product will be completed by the deadline set out by the stakeholder of the end of the school year.

15

# Continued Stakeholder Feedback

## Primary Stakeholder – Bruno Prijic

### 1. What are your thoughts on this final set of specifications?

I like how the sound of how the product will function, and am looking forward to seeing it completed.

### 2. How do you want these specifications to be prioritised?

I believe in function over form, so I would like if the priority is placed on having something that works as well as possible, but I still want it to look good.

### 3. Do you want any specifications to be changed?

I would like if I was kept updated and contacted regularly about the design and colour, and if I was shown a sample of each colour so I could see what looks best.

# Prioritised Specifications

## Essential

1.1 The product must successfully address my stakeholder’s issue by completely cleaning all dirt and mud off a Sea to Summit Ground Control tent peg. This is to be met through using some type of water jets to ensure no dried dirt or mud is left behind.
1.2 The product must be automated, requiring minimal user input. This will be achieved through a microcontroller such as an Arduino Uno, and electronic components and circuitry.
1.3 The product must have the capability to detect when a peg is inserted, automatically engaging the water jets. This is to be achieved by a laser tripwire system with a laser module and a photoresistor/LDR, to ensure maximum functionality in all conditions.
1.4 The product must be watertight to contain all used water and to protect all electronic components and circuitry. To meet this specification, I will explore production methods such as using 3D printing or laser cutting sheets of acrylic and gluing them together to ensure complete ingress and egress protection.

16

1.5 The product must be stable while in operation to ensure it does not tip over while in use. This must include a stable base with some type of rubber or similar footing to maintain stability on the sloped concrete at the location where the product is to be used and also to limit vibrations which may damage the product and make it more likely to tip.
1.6 The product must be environmentally friendly. This is to include minimal water and power consumption and recycling all consumed water through watering plants and other uses. This is to be optimised by ensuring the drain has small sprinkler holes to facilitate watering directly from the product. 1.7 The product must be robust and durable to maximise the lifespan of the product. This will be achieved through care during production and ensuring quality is always a priority.
1.8 The product must be completed by the deadline set out by the stakeholder of the end of the school year.

## Important

2.1 The product will have a system to turn itself on and off in order to conserve the longevity of the battery and reduce the frequency of recharging the battery.
2.2 The product will be no larger than 270mm x 180mm to ensure compactness and storability. This is derived from stakeholder consultation and feedback, where the directive has been that the product should be no larger than the rough dimensions of a 2L milk bottle.
2.3 The product will be highly versatile to ensure it suits as many use cases as possible. This will be achieved by ensuring the opening at the top of the product is designed to suit as many shapes and sizes of peg as possible, while still preventing unwanted ingress of objects and egress of water while in operation. Further, the product will be designed to work with a variety of water source systems.
2.4 The product will be intuitive and easy to use, with labelled and well-designed user inputs, to ensure a smooth user experience.
2.5 The product will be economical in its water and power consumption. This will be achieved through ensuring an efficient use of water with high pressure but low volume water jets, and power efficient components that are automatically turned off if not in use.
2.6 The product will be constructed out of a lightweight, cheap but versatile material such as 3D printed plastic. This will ensure a cost effective product that is easily developed and iterated.

## Desirable

3.1 The product is to be user friendly, with easily removed battery and water source connectors. This will be achieved using universal connectors and well-designed layouts that are intuitive and easy to operate.

17

3.2 The product is to require minimal set-up and assembly to ensure a smooth user experience, with the user only needing to connect a charged battery and connect the product to a water source. This will be met by ensuring the product is fully functional prior to delivery through comprehensive testing. 3.3 The product is to have a professional appearance and design, with no messy wiring. To fulfil this specification, I will frequently contact my stakeholder for feedback and input on design decisions, and by ensuring components are tidily laid out in an enclosure where possible.
3.4 The product is to be blue, grey or black in colour to fulfil my stakeholder’s requests. To best meet this specification, I will create a small scaled mock-up for each colour available to me to show my stakeholder how each colour will look, and obtain a final directive for which colour to proceed with.

## Minor

4.1 The product should be easily maintained by the user, with easy access to the battery for a smooth recharging process. It should also offer easy access to electronic components and circuitry to allow for easy troubleshooting.
4.2 The product should be portable, allowing the user to store it away inside their house and easily move it around. This will involve ensuring the product is lightweight and easily held.

These final specifications have been derived following initial stakeholder consultation regarding his issue and a conceptual phase exploring potential issues, followed by ongoing stakeholder feedback discussing their needs and requirements, and researching the location where the product will most frequently be used. This process has also involved speaking to his parents as secondary stakeholders to ascertain their requirements for the product, namely with a focus on the environmental and monetary impact of its operation. Following this process, I have drawn a list of attributes the product must have to best address my stakeholder’s issue, resulting in my final list of specifications to ensure the best possible outcome. I have then taken this finalised list of specifications to my stakeholder for feedback, including discussing the value of each specification. Following this feedback, I have prioritised each specification to ensure the final product is the best possible outcome to address his issue, with the most focus placed on the most essential specifications. Generally speaking, the specifications have been prioritised with the highest emphasis on ensuring an intuitive, smooth user experience by placing specifications focussing on functionality the highest, with less emphasis on aesthetic and other minor details. Again, this is to ensure the best product that best addresses my stakeholder’s issue.

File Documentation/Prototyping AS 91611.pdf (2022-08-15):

jb16214 | Prototyping AS 91611 | 13CTE

1

# Prototyping AS 91611

# Tools, Materials and Components

In order to develop my prototype for my Peg Cleaner project I used a large variety of tools, materials, and processes to produce a proof-of-concept and through to a working prototype, both materially and electronically. Some of these included:
Tools:
- Ultimaker 3D printer
- VLS Laser Cutter/Engraver
- CamCut PCB Miller
- AutoCAD
- Adobe Illustrator
- Adobe InDesign
- EasyEDA
- 2D Design
Materials:
- Acrylic
- PLA Filament
- Copper/fibreglass sheets Processes:
- 3D printing
- Laser cutting & laser engraving
- PCB milling
- Soldering
I decided to primarily use 3D printing to produce my models as it allowed me the flexibility in designs I needed, such as instead of laser cutting a 2D net of a box and gluing it together, I could simply design a 3D model of the box and print it, only needing to process the result if I used support material. If I wanted to laser cut acrylic to produce a shape such as the cylinder I had for the peg cleaner itself, I would have either had to redesign into a workable 2D shape or use a thermoplastic bending machine to attempt to produce something resembling a cylinder, and I would have never been able to produce the rounded spherical shape I had at the bottom of the ‘bottle’ to streamline the drainage system.
My initial plan to produce and fabricate my PCB was to use our previous Voltera prototyping machine to validate that the circuit was fully functional on a proper board and not just on the breadboard, after which I would have it fabricated by a prototyping company such as JLCPCB. Multiple aspects of the plan changed however, and I ended up not having the time to realistically send my completed PCB design off and wait for it to arrive, and also we moved away from the Voltera printed ink circuit boards back to a CNC miller. Therefore, my final PCB being used in my project was produced using the school’s CNC miller.

2

# Testing and Stakeholder Feedback


Testing | Evaluation/Description | Result of testing
| With my first test print to evaluate whether my interlocking design would work satisfactorily, I ran into issues as I did not include tolerance in my designs, which meant the models did not interlock as intended. This is likely as 3D printing is an additive process meaning that material is added rather than taken away, meaning there is a possibility for excess material, compared to the possibility for less material than expected with a subtractive process like laser cutting or CNC milling. Also, it is possible that the model has slightly warped or expanded as it does not cool instantly, all resulting in a pair of models which do not interlock. As a result of this testing, I learnt that I needed to account for some tolerance in my designs prior to attempting to print them if I wanted to create interlocking pieces, and so I added 1mm of tolerance between the ‘plates’, and 0.5mm of tolerance between the edges. After re-testing this, I found that this went too far the other way and resulted in pieces that were too loose, and so I tried a tolerance of 0.5mm between plates and 0.25mm between the edges, which worked perfectly, and which met my stakeholder’s standards.


Figure 1: Far too much tolerance


Figure 2: Perfect amount of tolerance

Commit:
https://github.com/JamesNZL/13CTE/commit/aa8a77da3e9661fec6106ba259 78a57e9216726c#diff-478d489bfcf667342e1abaab833bd111caf388a7ed8cff49d9b7110c752adfb3 (https://github.com/JamesNZL/13CTE/commit/aa8a77da3e9661fec6106ba25978a57e9216726c)

3


I then tested my measurements for my component mounting positions, which all fit well.

Testing taper angles to ensure a perfect fit between interlocking pieces, as in theory somewhere along the tapered edge would be the best possible tolerance level. To test this, I designed pieces with an extruded peg with its four edges tapered, and a female ‘socket’ with straight edges. In the image, the green lines from right to left represent taper values of -1 and -0.75 degrees which both overlap with the edge of the socket, and then -0.7, -0.65, -0.5 and 0 degrees of taper, all of which fall within the edge of the socket.

After 3D printing all the models and having my stakeholder test their performances, I found that the piece tapered at -0.65 degrees fit the best, and therefore I added a taper of -0.65 to all my interlocking faces.

Testing: https://youtu.be/0a5CKYdv350

Commit:
https://github.com/JamesNZL/13CTE/commit/7d831fed5e 6855c02678fc288ef6d3c090c2dea4 (https://github.com/JamesNZL/13CTE/commit/7d831fed5e6855c02678fc288ef6d3c090c2dea4)

4


I then tested my Cura 3D printing settings to see if I could improve them to get better results, particularly as my support material was extremely difficult to remove and often resulted in damage to my actual part. In this example of testing, I changed the support z distance and the support density in Cura, from 0.1mm to 0.2mm of z distance (i.e. the vertical spacing between the part and the start of the support material, a higher z distance means less adhesion), and a reduction of support density from 20% to 10%.

As can be seen in the images, the support material is now much less solid than that seen in the images above such as with the test print using gold filament, which meant these supports were extremely easy to remove, and did not negatively impact the quality of the final part.

I then tested the measurements for my connector mount, in order to verify that it would all fit and mount correctly. I found that there was insufficient clearance in the top of the model, which required quite a bit of filing to finally result in a very tight fit.

https://github.com/JamesNZL/13CTE/commit/27d3916e76 b9ce227ab2e8ded5c193118664894a (https://github.com/JamesNZL/13CTE/commit/27d3916e76b9ce227ab2e8ded5c193118664894a)

As a result of this testing, I removed 1.25mm from all sides of the connector mount, and reprinted the part to see if that was sufficient. After re-testing, I found there was still adjustments needed for an optimal fit, and continued to adjust the clearances and tolerances in the model, such as in

5


https://github.com/JamesNZL/13CTE/commit/66ca306ef5 5cf26e394b91cc1458b539f51610aa. (https://github.com/JamesNZL/13CTE/commit/66ca306ef55cf26e394b91cc1458b539f51610aa)

Eventually, I refined the model to a point where the connectors mounted perfectly:


Figure 3: View from 'exterior' of box


Figure 4: View from 'interior' of box

6


Alongside my testing of the clearances for my connector mount, I was also testing the measurements for the water level sensor to work as efficiently as possible, as I could easily fit both parts into the same print, meaning I could print both models at the end of the day and test them both the day after, instead of doing it one at a time.


On my first version of my model for the water level sensor, I found that I had insufficient clearance for the bottom of the sensor, which required me to manually remove roughly 1.5mm of material with a knife before it fit tightly.

As a result of my testing, I removed 1.25mm from the bottom of the model:
https://github.com/JamesNZL/13CTE/commit/e7651b4972 0eb194210a46844635a350b228c86a (https://github.com/JamesNZL/13CTE/commit/e7651b49720eb194210a46844635a350b228c86a)

After re-testing this updated model, I found that the clearances were massively improved, and would be acceptable for my final print.

7


After I found performant values for tolerance in my interlocking lid pieces and after I applied the changes to my interlocking base components, I printed a skeleton just to verify that it was all acceptable, which it was.

As a result of testing these components however, I realised that my design for the watering rose would need to be redesigned, as for the model to print as a singular piece, it would need to be filled with support material, which would ultimately be far too difficult to remove as the only opening would be the 15mm hole at the top for the solenoid threading.


Because of this testing, I separated the rose into two components which interlock together, meaning that there is no longer a void which needs to be filled with support material.


8


Testing the alignment of the mounting holes for the Arduino, one of the holes is incorrectly spaced

Fixed by
https://github.com/JamesNZL/13CTE/commit/4dc54e848215b8 9809f9dd6c7754f405596d120c (https://github.com/JamesNZL/13CTE/commit/4dc54e848215b89809f9dd6c7754f405596d120c)

Testing the threading for the modelled solenoid valve coupling

Perfect fit, no adjustments required

9


10


Result of final box lid, with buttons and indicator LED mounted with holes for the acrylic button label inserts

Mounted female hose couplings

11

Cloudy button labels as a result of glue application

Given more time available, I would have liked to have tested this with a wider range of glue options and quantities, in order to have the best result.


However, at this stage I was quite pressed for time as a result of the disruption caused this year meaning I had much less time available to physically be prototyping and testing, and after I found that using a glue stick would not be sufficient to reliably keep the acrylic labels in, I hastily used superglue, without ensuring an even application, resulting in the cloudy underside. Mounting of water level sensor in final printed prototype


12


Mounting of drain solenoid valve in final prototype

13


Completed layout of ‘plumbing’ system for water jets – the water all passes through the ‘control box’ from the garden spigot on its way to the water jets, where a solenoid valve controls whether the water is flowing or not.

The hoses are all fitted with quick-disconnects at logical breakpoints as requested and decided by my stakeholder to enable easy storage.


14

# Fitness for Purpose of Prototype

Figure 5: Final prototype
Evaluating the results of all my testing and prototyping, involving continual stakeholder consultation and feedback, the final prototype I developed was highly successful in meeting my stakeholder’s brief and specifications, both physically and electronically. It is also successful in addressing the intended environment(s) where it will be used, being designed for an outdoors usage with features such as having non-slip rubber footing, to improve robustness and also prevent damage to the product itself if used on concrete. The user inputs are handled by durable industrial pushbuttons with an IP rating of IP65 for sufficient ingress protection, again to meet another of my stakeholder’s specifications. Evaluating directly against the attributes provided in the stakeholder’s brief, I can again see that this prototype is very successful in being fit for purpose:
Attributes | Evaluation
Physical
Lightweight. The product should be made out of 3D printed plastic or a similar lightweight and cheap material, with the added benefit of being easily manipulated and adjusted. | My prototype fully fulfils this provided attribute, consisting primarily of 3D printed models with some small laser cut furnishings, all lightweight and easily manufacturable, with extremely affordable costs for materials.
Blue, grey or black. The product should be made out of or finished in a blue, grey or black colouring. | My prototype is 3D printed with blue filament as per my stakeholder’s request, though does use two different colours as the light blue filament was used up. After consulting with my stakeholder, he said that it was a non-issue as it was still a prototype, was still a blue coloured filament, and as they were two different components, where the water blaster is entirely light blue, and the control box is entirely dark blue (the dark blue piece on the water blaster is hidden when fully inserted into the base).

15

Professional. The product should be professional in appearance, with no messy wiring. | This attribute could and would be improved upon in future iterations, either by exploring a wireless method of transmitting information with a battery pack in the water blaster, or by looking at ways to better manage the wiring, such as with cable sleeving. After consulting with my stakeholder however, he said that he didn’t mind, and that he particularly liked how easy it was to disconnect the two components due to the connector and quick disconnect in the hose.
Robust and durable. The product should be made with quality in mind, to maximise the lifespan of the product. | My prototype has been designed with multiple features to increase the lifespan of the product and to improve its durability and robustness, such as the rubber feet on the water blaster, securing wire connections/terminations in place with superglue to prevent shearing and fatigue, and using industrial grade components such as the pushbuttons and LED indicator to maximise the service life of my product.
Compact and storable. The product should be no larger than the rough dimensions of a 2L milk bottle to ensure storability and sleekness. | Although I was unable to fit it all entirely into a single physical component, after working together with my stakeholder to finalise a conceptual design I was able to design a two-part system to meet the purpose and the specifications, both of which meet the size requirements. My stakeholder was happy as although there are two separate components, he preferred to have two modular components over one large all-in-one solution.

Functional
Automated. The product
should automatically
detect once a peg has
been inserted and begin
the cleaning process. It
should also automatically
drain contained water if
necessary, | and
automatically power off if left unattended.

My prototype fully meets this functional attribute through its electronics and control system, using multiple sensors to guarantee performance. My prototype uses a laser tripwire with an LDR and a laser diode to detect when a peg has been inserted, triggering the solenoid in the control unit to allow water to flow through the jet blasters. It also has a water level sensor embedded in the side of the water blaster in order to detect a potential overflow, and automatically triggers the drain solenoid to avoid the possibility. Through its embedded software, it automatically begins/resets a 3 minute countdown after each user input, where if there have been no inputs after the 3 minutes, the device automatically turns itself off.
Effective. The product should be capable of completely addressing the issue and cleaning all debris off the peg. | My prototype uses sprinklers designed for watering gardens, with an adjustable screw-head that controls the size of the output, allowing me to control whether it produces a single powerful jet, or a fine mist. When configured properly, the jet stream produced is more than capable of completely cleaning a dirty tent peg, which both I and my stakeholder successfully tested.
Versatile. The product should be adaptable for a variety of locations and water supply systems. | My prototype can be connected to any water source provided it has suitable pressure and has a ½” male threading to fit into the receiving end of my control unit, allowing for a wide variety of water supply systems.
Stable. The product should feature a stable base with rubber or similar high-friction footing to maintain stability on sloped concrete. | As evaluated above in the point for ‘robust and durable’, my prototype has rubber non-slip footing on both components for stability and protection, especially as the product is likely to be used in an outdoors environment, and potentially on concrete.


16

Social
Eco-friendly. The product should be economical in its water and power consumption, and should contain all water used to be repurposed. | My prototype fully addresses this attribute by using extremely efficient garden sprinklers configured to produce a single, high pressure jet stream, with high pressure but low volume. Further, the prototype features a drain solenoid valve in the bottom of the water blaster to retain all water used until told to drain by the user through the drain button, unless the water blaster is about to overflow, in which case it will automatically drain just enough water to be at a safe level again.
Intuitive. The product should be intuitive to use, with logical and user-friendly layouts and inputs. | My prototype is extremely user-friendly and intuitive, with a connector and quick disconnect for all the connections between the two modular components, and labelled buttons and an indicator LED which will display different colours in different states (i.e. blinking, solid, etc.) in order to communicate information to the user.
User | friendly. | The
product should be easily
maintained, being easily
connected to a water
source | and | easily
recharged.

As discussed above in ‘versatile’, my prototype is easily connected to any water source provided the user has the correct male fitting to connect with my control unit. It is also easily maintained with a snap-on lid for the control box, allowing the user easy access to the electronics if needed. The prototype also checks the battery voltage on start-up to alert the user if the battery is getting low, or will automatically turn off if the battery level is critical. To recharge the battery, the user simply needs to open the box lid and disconnect the battery’s connector, and recharge it as a normal LiPo battery.

Figure 6: Control unit interior & battery connector
Minimal set up. The
product | should | not
require any additional set up other than connecting
a water source and
ensuring the battery is
charged.

My prototype fully meets this attribute, as its entire start-up process is:
1. Connect the two modules together, using the wired connector and hose fittings
2. Connect the control unit to the water source
3. Press the green on button

17

# Iterative Development of Prototype

As discussed within the ‘Testing and Stakeholder Feedback’ section above, throughout my prototyping and development process I have been continually making changes and improvements to my design and making decisions in order to produce a better final result, and constantly consulting my stakeholder for feedback and input in order to verify that I was moving in the right direction as per their intent. Some of these changes were because I realised my initial modelled design would not work or would produce unsatisfactory results, such as the redesign I did for the watering rose, and others were for general improvements to the quality of the prototype, such as redesigning the brace around the drain solenoid valve in order to improve its structural integrity and strength. For the most part however, the final prototype closely resembled the conceptual design I developed alongside my stakeholder, and resulted in a product that fully meets their specifications and is fully fit for purpose.

# Evaluation of Materials Selection

I decided early on in the development process to proceed with a design that was centred upon a 3D printed prototype, as it allowed for rapid prototyping and ease of design iteration and testing, as well as being affordable and repeatable. If I had chosen a different set of materials or techniques to produce my design, such as milling out a block of wood or piecing together sheets of laser cut acrylic, the lead time for prototyping would have been significantly longer and would have likely resulted in a prototype that was not even half-completed by the end of the year, and even more so with the even more limited time I had available to me to actually produce physical work in school this year due to the restrictions and disruptions due to COVID. By choosing to use 3D printing, I could easily iterate and develop my 3D model and design at home, and come in to school and start a skeletonised, reduced test print first thing in the morning, meaning I would usually have a completed test piece by our class period. This meant I could easily develop and iterate my design and continually have new things to show my stakeholder and to get feedback on, all of which contributed to the highly successful final prototype I produced.
If I had decided to use sheets of acrylic and laser cut them, I would have required a completely different design as it would have been far too difficult to produce a cylindrical shape, and would ultimately have resulted in a far messier final product with all the glue I would have needed to piece the product together.

18

# Evaluation of Prototype against Specifications

Specifications | Evaluation
Essential | This evaluation references all previously included evidence, and builds upon my evaluation of my stakeholder’s specified attributes.

1.1 The product must successfully address my stakeholder’s issue by completely cleaning all dirt and mud off a Sea to Summit Ground Control tent peg. This is to be met through using some type of water jets to ensure no dried dirt or mud is left behind.

My prototype fully and entirely fulfils these essential specifications of my stakeholder’s brief, having been designed specifically to address the brief with continual and comprehensive stakeholder consultation and feedback throughout the development and prototyping process.
As discussed above, my prototype uses an advanced control system with a variety of sensors and comprehensive embedded software in order to deliver the desired results, using solenoid valves controlled electronically in order to control the water jets that clean the tent pegs.
My product is fully automated, with a MOSFET control circuit that allows the Arduino to turn itself off, allowing me to have a 3 minute sleep timer, where after 3 minutes of user inactivity, the Arduino automatically turns itself off in order to conserve battery life. As previously discussed, other circuity includes a laser tripwire in order to facilitate an automated trigger for the water jets, and push buttons to control on/off and manual drain functionality.
My product is entirely watertight, with a single 3D-printed model acting as the body for the water level sensor, with the egress point being the input of my drain solenoid valve, which only allows water to pass through while the user is pressing the drain button or while the water level is above the water level sensor’s emergency trigger point.
My product is designed to be stable on all surfaces with a tri-footed footprint to maximise stability, with non-slip rubber footing to ensure grip and traction on all surfaces. Further, as the drain solenoid valve is effectively the only significant mass in the water blaster module, it is heavily bottom-weighted, further improving the stability of the product.

1.2 The product must be automated, requiring minimal user input. This will be achieved through a microcontroller such as an Arduino Uno, and electronic components and circuitry.
1.3 The product must have the capability to detect when a peg is inserted, automatically engaging the water jets. This is to be achieved by a laser tripwire system with a laser module and a photoresistor/LDR, to ensure maximum functionality in all conditions.
1.4 The product must be watertight to contain all used water and to protect all electronic components and circuitry. To meet this specification, I will explore production methods such as using 3D printing or laser cutting sheets of acrylic and gluing them together to ensure complete ingress and egress protection.
1.5 The product must be stable while in operation to ensure it does not tip over while in use. This must include a stable base with some type of rubber or similar footing to maintain stability on the sloped concrete at the location where the product is to be used and also to limit vibrations

19

which may damage the product and make it more likely to tip.

As previously discussed, the drain solenoid valve will only release the water contained in the water blaster while the user is pressing the drain button, or while the water level inside the water blaster is at a configured emergency level. Further, my selection for the water jets means that the water consumption of my product is minimal, with a high pressure but low volume water jet to clean the pegs. The prototype also has a watering rose built into the bottom of the drain, allowing for the device to be used directly as an imitation watering can.
My prototype was also completed in time to meet the stakeholder’s deadline, having been completed by the end of Term 3.

1.6 The product must be environmentally friendly. This is to include minimal water and power consumption and recycling all consumed water through watering plants and other uses. This is to be optimised by ensuring the drain has small sprinkler holes to facilitate watering directly from the product.
1.7 The product must be robust and durable to maximise the lifespan of the product. This will be achieved through care during production and ensuring quality is always a priority. 1.8 The product must be completed by the deadline set out by the stakeholder of the end of the school year.
Important
2.1 The product will have a system to turn itself on and off in order to conserve the longevity of the battery and reduce the frequency of recharging the battery.

As discussed above in my evaluation of the stakeholder’s ‘essential’ specifications, my product uses a MOSFET control circuit to allow the Arduino to turn itself off. This means that I was able to implement time-out and battery level monitoring systems in order to conserve battery life and protect the battery from discharging below its safe voltage threshold. The time-out system works by restarting a 3 minute timeout on each user input, such that once the inactivity period is equal to 3 minutes, the device automatically powers off. The prototype also includes a battery monitoring system, where each time the device powers on it will automatically calculate the voltage of the battery, and if it is within the ‘low battery’ range it will flash
red on the indicator LED, or if it is ‘critical’, it will flash red
then automatically power off in order to protect the LiPo
cells.
My product is designed to be as versatile as possible, with an insert slot designed to accept as many types of pegs as is practical (shown right). It also only requires a ½” male

2.2 The product will be no larger than 270mm x 180mm to ensure compactness and storability. This is derived from stakeholder consultation and feedback, where the directive has been that the product should be no larger than the rough dimensions of a 2L milk bottle.
2.3 The product will be highly versatile to ensure it suits as many use cases as possible. This will be achieved by ensuring the opening at the top of the product is designed to suit as many shapes and sizes of peg as possible, while still preventing unwanted ingress of objects and egress of water while in operation. Further, the product will be designed to work with a variety of water source systems.


20

2.4 The product will be intuitive and easy to use, with labelled and well-designed user inputs, to ensure a smooth user experience.

threading for the water supply, meaning it will effectively accept any water source system provided it has enough water pressure and can be fitted with a ½” coupling. My prototype has labelled and colour-coded buttons for user inputs for an intuitive and user-friendly interface, with a dynamically controlled RGB indicator LED to communicate information and statuses to the user.
My prototype is primarily designed and produced with 3D printed plastic, which has allowed me to rapidly prototype changes and iterations in order to improve my prototype and produce a better outcome that better meets the brief and is more fit for purpose.

2.5 The product will be economical in its water and power consumption. This will be achieved through ensuring an efficient use of water with high pressure but low volume water jets, and power efficient components that are automatically turned off if not in use.
2.6 The product will be constructed out of a lightweight, cheap but versatile material such as 3D printed plastic. This will ensure a cost effective product that is easily developed and iterated.
Desirable
3.1 The product is to be user friendly, with easily removed battery and water source connectors. This will be achieved using universal connectors and well-designed layouts that are intuitive and easy to operate.

My prototype uses a variety of components designed to make it as user friendly as possible, including using quick-disconnect fittings for the plumbing system for quick assembly and disassembly, a MOLEX keyed connector to electrically connect the two modules together, and an XT60 battery connector to allow easy removal of the battery from the control box for recharging.
It is also designed to be as simple as possible to set up and start-up, with the entire process consisting only three steps:
1. Connect the two modules together, using the wired connector and hose fittings
2. Connect the control unit to the water source
3. Press the green on button
With the exception of the wires to connect the two modules together, I would agree with my stakeholder’s opinion that the final prototype is relatively professional in its design and appearance, with the majority of the control circuitry inside the control unit. With more time to iterate and develop the prototype I would have liked to look at exploring options for a wireless connection between the two modules or perhaps

3.2 The product is to require minimal set-up and assembly to ensure a smooth user experience, with the user only needing to connect a charged battery and connect the product to a water source. This will be met by ensuring the product is fully functional prior to delivery through comprehensive testing.
3.3 The product is to have a professional appearance and design, with no messy wiring. To fulfil this specification, I will frequently contact my stakeholder for feedback and input on design decisions, and by ensuring components are tidily laid out in an enclosure where possible.
3.4 The product is to be blue, grey or black in colour to fulfil my stakeholder’s requests. To best meet this specification,

21

I will create a small scaled mock-up for each colour available to me to show my stakeholder how each colour will look, and obtain a final directive for which colour to proceed with. | moving from an Arduino board to just a standalone ATMEGA to miniaturise the control circuitry, or looking at getting cable sleeving to clean up the wiring.

Minor
8.1 The product should be easily maintained by the user, with easy access to the battery for a smooth recharging process. It should also offer easy access to electronic components and circuitry to allow for easy troubleshooting. | As already discussed, the battery and the rest of the electronics is easily accessed just by taking off the snap-on lid of the control unit’s enclosure, and is easily disconnected as it uses a standard XT60 LiPo battery connector. The product is highly portable and modular, being connected to each other only through two connectors, a MOLEX connector for the electronics and a ½” threading for the hosing. The rest of the prototype is also interlocking, with a base that is easily removed for easy storage.

8.2 The product should be portable, allowing the user to store it away inside their house and easily move it around. This will involve ensuring the product is lightweight and easily held.

Evaluating my final prototype against the specifications provided to me by my stakeholder, I can see that my design and final outcome is highly successful in addressing the brief and is fully fit for purpose, and is entirely in line with the stakeholder’s intent. This was also verified throughout the design, development and prototyping stages by continual stakeholder consultation, obtaining feedback on potential changes and design decisions to produce the best possible outcome.

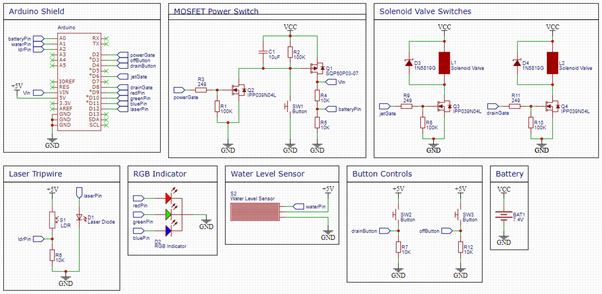
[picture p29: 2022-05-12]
Documentation/Photo Evidence/schematic.png

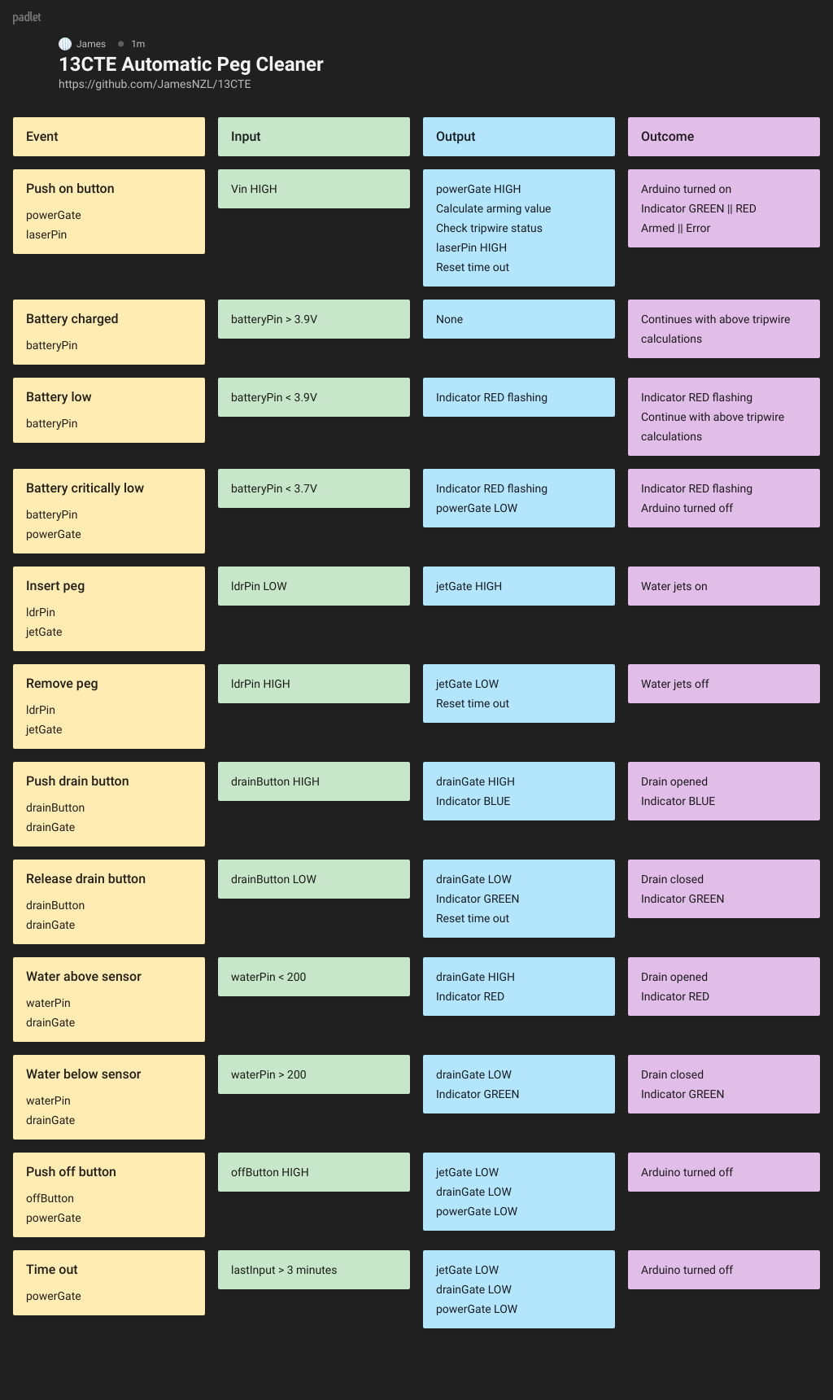
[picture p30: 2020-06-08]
Software Algorithm.png

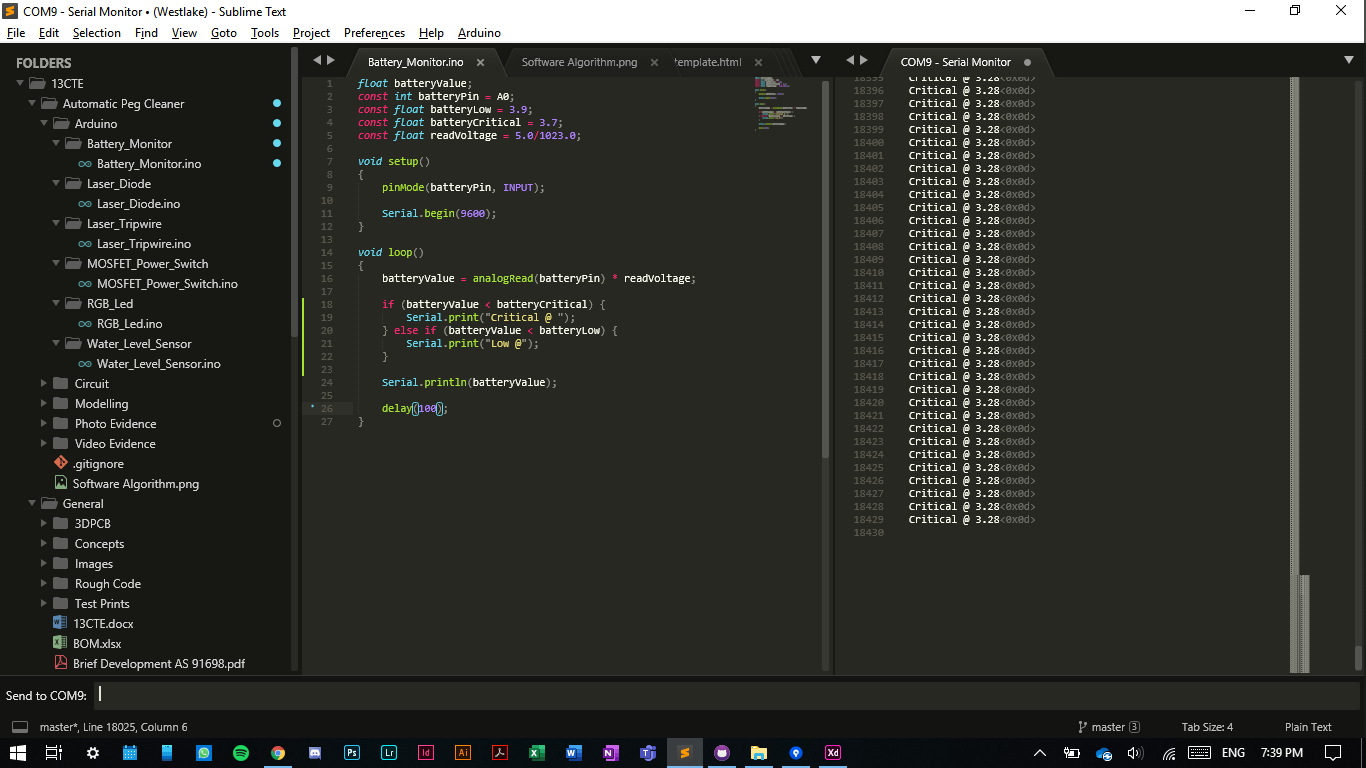
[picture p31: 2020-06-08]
Documentation/Photo Evidence/Critical battery.png

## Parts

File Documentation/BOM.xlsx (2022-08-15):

Index | Quantity | Part Number | Manufacturer Part Number | Description | Customer Reference | Available | Backorder | Unit Price | Extended Price NZD
1 | 2 | NSL-6112-ND | NSL-6112 | PHOTOCELL |  | 2 | 0 | 3 | 6.00
2 | 3 | 445-173437-1-ND | FG26X7R1E106KRT06 | CAP CER 10UF 25V X7R RADIAL |  | 3 | 0 | 1.41 | 4.23
3 | 10 | RNF14FTD10K0CT-ND | RNF14FTD10K0 | RES 10K OHM 1/4W 1% AXIAL |  | 10 | 0 | 0.133 | 1.33
4 | 10 | RNF14FTD100KCT-ND | RNF14FTD100K | RES 100K OHM 1/4W 1% AXIAL |  | 10 | 0 | 0.133 | 1.33
5 | 10 | RNF14FTD249RCT-ND | RNF14FTD249R | RES 249 OHM 1/4W 1% AXIAL |  | 10 | 0 | 0.133 | 1.33
6 | 5 | 1655-1922-1-ND | 95SQ015 | DIODE SCHOTTKY 15V 9A DO201AD |  | 5 | 0 | 1.2 | 6.00
7 | 4 | IPP039N04LGXKSA1-ND | IPP039N04LGXKSA1 | MOSFET N-CH 40V 80A TO220-3 |  | 4 | 0 | 2.19 | 8.76
8 | 2 | SQP50P03-07_GE3-ND | SQP50P03-07_GE3 | MOSFET P-CH 30V 50A TO220AB |  | 2 | 0 | 3.61 | 7.22

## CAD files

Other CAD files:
Modelling/Automatic Peg Cleaner.dwg

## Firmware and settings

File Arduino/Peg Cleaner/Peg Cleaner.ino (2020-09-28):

int ldrValue;
int triggerAt;
int waterMinimum = 200;

bool ldrConnected = true;
bool jetsEngaged = false;
bool waterDanger = false;
bool buttonPressed = false;
bool drainEngaged = false;
bool terminateAlert = false;
bool pinState = HIGH;

unsigned long currentTime;
unsigned long lastAction = 0;
unsigned long lastAlert = 0;
unsigned long terminateTime = 180000;
unsigned long terminateNotify = 15000;

const float batteryLow = 3.9;
const float batteryCritical = 3.7;

const int batteryPin = A0;
const int waterPin = A1;
const int ldrPin = A2;
const int powerGate = 2;
const int offButton = 3;
const int drainButton = 4;
const int jetGate = 6;
const int drainGate = 8;
const int redPin = 9;
const int greenPin = 10;
const int bluePin = 11;
const int laserPin = 12;
const int testIterations = 5;
const int maximumValue = 1023;

const unsigned long alertDelay = 500;

void setup() 
{
	pinMode(batteryPin, INPUT);
	pinMode(waterPin, INPUT);
	pinMode(ldrPin, INPUT);
	pinMode(offButton, INPUT);
	pinMode(drainButton, INPUT);

	pinMode(powerGate, OUTPUT);
	pinMode(jetGate, OUTPUT);
	pinMode(powerGate, OUTPUT);
	pinMode(redPin, OUTPUT);
	pinMode(greenPin, OUTPUT);
	pinMode(bluePin, OUTPUT);
	pinMode(laserPin, OUTPUT);
	
	digitalWrite(powerGate, HIGH);

	indicatorControl(HIGH, LOW, LOW);
	batteryCheck();
	tripwireSetup();
	tripwireCheck();
}

void loop() 
{
	currentTime = millis();
	
	jetsEngaged = tripwireEngage();
	drainEngaged = drainEngage();
	
	if (jetsEngaged == true || drainEngaged == true) {
		terminateAlert = checkTurnOff(LOW, LOW, pinState);
	}

	else {
		terminateAlert = checkTurnOff(LOW, pinState, LOW);
	}

	if (jetsEngaged == false && drainEngaged == false && ldrConnected == true) {
		indicatorUpdate(LOW, HIGH, LOW);
	}
}

void batteryCheck()
{
	float batteryValue = analogRead(batteryPin) * (5.0 / 1023.0);

	if (batteryValue < batteryLow) {
		indicatorAlert(HIGH, LOW, LOW);
	}

	else if (batteryValue < batteryCritical) {
		indicatorAlert(HIGH, LOW, LOW);

		digitalWrite(powerGate, LOW);
	}
}

void tripwireSetup()
{
	int testTotal = 0;

	digitalWrite(laserPin, LOW);

	for (int i = 1; i <= testIterations; i++) {
		int fluctuation = abs(analogRead(ldrPin) - (testTotal/i));

		if (fluctuation > 10) {
			break;
		}

		testTotal += analogRead(ldrPin);
	}

	digitalWrite(laserPin, HIGH);

	int disarmedValue = testTotal / testIterations;
	triggerAt = (maximumValue + disarmedValue) / 2;
}

void tripwireCheck()
{
	ldrValue = analogRead(ldrPin);

	while (ldrValue < triggerAt) {
		ldrValue = analogRead(ldrPin);

		indicatorUpdate(HIGH, LOW, LOW);
		tripwireSetup();
		checkTurnOff(pinState, LOW, LOW);
	}
	
	if (ldrValue > triggerAt) {
		indicatorControl(LOW, HIGH, LOW);
	}
}

bool tripwireEngage()
{
	ldrValue = analogRead(ldrPin);

	if (ldrValue == 0) {
		ldrConnected = timeOut(ldrConnected, true);

		digitalWrite(jetGate, LOW);

		indicatorUpdate(HIGH, LOW, LOW);
	}

	else if (ldrValue <= triggerAt) {
		jetsEngaged = timeOut(jetsEngaged, false);
		
		digitalWrite(jetGate, HIGH);

		indicatorUpdate(LOW, LOW, HIGH);

		return jetsEngaged;
	} 

	else {
		jetsEngaged = timeOut(jetsEngaged, true);
		
		digitalWrite(jetGate, LOW);

		return jetsEngaged;
	}
}

bool drainEngage()
{
	int waterValue = analogRead(waterPin);
	int drainInput = digitalRead(drainButton);

	if (waterValue > waterMinimum || drainInput == HIGH) {
		waterDanger = timeOut(waterDanger, false);
		buttonPressed = timeOut(buttonPressed, false);

		digitalWrite(jetGate, LOW);
		digitalWrite(drainGate, HIGH);

		if (drainInput == HIGH) {
			indicatorUpdate(LOW, LOW, HIGH);
		} 

		else {
			indicatorUpdate(HIGH, LOW, LOW);
		}

		return true;
	}

	else {
		waterDanger = timeOut(waterDanger, true);
		buttonPressed = timeOut(buttonPressed, true);

		digitalWrite(drainGate, LOW);

		return false;
	}
}

void indicatorControl(byte redOutput, byte greenOutput, byte blueOutput)
{
	digitalWrite(redPin, redOutput);
	digitalWrite(greenPin, greenOutput);
	digitalWrite(bluePin, blueOutput);
}

void indicatorUpdate(byte redOutput, byte greenOutput, byte blueOutput) {
	if (terminateAlert == false) {
		indicatorControl(redOutput, greenOutput, blueOutput);
	}

}

void indicatorAlert(byte redOutput, byte greenOutput, byte blueOutput)
{
	for (int i = 0; i < 5; i++) {
		indicatorControl(redOutput, greenOutput, blueOutput);
		delay(alertDelay);
		indicatorControl(LOW, LOW, LOW);
		delay(alertDelay);
	}
}

bool timeOut(bool previousState, bool testFor)
{
	if (previousState == testFor) {
		lastAction = currentTime;
	}

	return !testFor;
}

bool checkTurnOff(byte redOutput, byte greenOutput, byte blueOutput)
{
	currentTime = millis();
	int offInput = digitalRead(offButton);

	terminateAlert = false;

	if (offInput == HIGH) {
		shutDown();
	}

	if ((currentTime - lastAction) >= terminateTime) {
		shutDown();
	}

	else if ((currentTime - lastAction) >= (terminateTime - terminateNotify)) {
		terminateAlert = true;

		if ((currentTime - lastAlert) >= alertDelay) {
			indicatorControl(redOutput, greenOutput, blueOutput);

			pinState = !pinState;
			lastAlert = currentTime;
		}
	}

	return terminateAlert;
}

void shutDown()
{
	while (true) {
		indicatorControl(LOW, LOW, LOW);
		digitalWrite(jetGate, LOW);
		digitalWrite(drainGate, LOW);
		digitalWrite(powerGate, LOW);
	}
}

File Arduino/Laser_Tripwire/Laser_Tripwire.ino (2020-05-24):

int sensorValue;                                            // variable for current analogue reading from LDR
int disarmedValue;                                          // variable that records the analogue reading from LDR when laser is disengaged ('disarmed' value)
int triggerAt;                                              // variable for what LDR reading to 'trigger' tripwire at (Let 'disarmed' value be 500, 'armed' value be max of 1000, triggerAt would be 1000 - 500/2 = 1000 - 250 = 750)
int testTotal;                                              // iterative variable to record total of (testIterations) readings from LDR when initialising
const int sensorPin = A0;                                   // LDR 'signal' pin
const int laserPin = 12;                                    // laser pin
const int redPin = 9;                                       // rgb module red pin
const int greenPin = 10;                                    // rgb module blue pin
const int bluePin = 11;                                     // rgb module blue pin
const int testIterations = 5;                               // number of readings to perform when initialising
const int maximumValue = 1023;                              // maximum reading possible from LDR, therefore maximum reading when laser is 'armed'

void setup() {
	pinMode(sensorPin, INPUT);                                // defines (sensorPin) as an input pin
	pinMode(laserPin, OUTPUT);                                // defines (laserPin) as an output pin
	pinMode(redPin, OUTPUT);                                  // defines (redPin) as an output pin
	pinMode(greenPin, OUTPUT);                                // defines (greenPin) as an output pin
	pinMode(bluePin, OUTPUT);                                 // defines (bluePin) as an output pin
	
	Serial.begin(9600);                                       // initialise serial monitor at 9600 baud

	digitalWrite(laserPin, LOW);                              // disengage laser for preliminary sensor reading

	for (int i = 0; i <= (testIterations - 1); i++) {         // perform the following actions (testIterations) times
		testTotal += analogRead(sensorValue);                   // add current analogue reading from LDR to existing (testTotal) value
	}

	digitalWrite(laserPin, HIGH);                             // engage laser tripwire

	disarmedValue = testTotal / testIterations;               // set (disarmedValue) equal to average of the (testIterations) tests
	triggerAt = (maximumValue + disarmedValue) / 2;           // set (triggerAt) to mid point between 'armed' and 'disarmed' / 'triggered'

	sensorValue = analogRead(sensorPin);                      // read current value from LDR

	if (sensorValue < triggerAt) {                            // if analogue reading from LDR indicates the tripwire is disarmed, do the following
		digitalWrite(redPin, HIGH);                             // turn red LED on
		digitalWrite(greenPin, LOW);                            // turn green LED off
		digitalWrite(bluePin, LOW);                             // turn blue LED off
	}
	
	else if (sensorValue > triggerAt) {                       // if analogue reading from LDR indicates the tripwire is armed, do the following
		digitalWrite(redPin, LOW);                              // turn red LED off
		digitalWrite(greenPin, HIGH);                           // turn green LED on
		digitalWrite(bluePin, LOW);                             // turn blue LED off
	}
}

void loop() {
	sensorValue = analogRead(sensorPin);                      // update (sensorValue) to analogue reading from LDR now that the tripwire is armed
	
	while (sensorValue >= triggerAt) {                        // until the analogue reading has dropped below 'activation' threshold, do the following
		sensorValue = analogRead(sensorPin);                    // update (sensorValue)
		Serial.println(sensorValue);                            // print current value to serial monitor (for debugging)
	}

	Serial.print("Triggered @ ");                             // if tripwire is broken, print 'Triggered' to serial monitor
	Serial.println(sensorValue);
}

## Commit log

2020-03-10 Bug fix
    sensorValue is still set to initial value of 0 when entering while loop for first time, therefore triggers immediately
    [Laser_Tripwire.ino]
2020-03-10 Code fixes
    Added type to constant variables, corrected legacy variable name
    [Laser_Tripwire.ino]
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2020-03-10 Corrected maximum analogue reading
    [Laser_Tripwire.ino]
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2020-03-25 Added RGB LED to confirm tripwire is functioning
    Red LED = tripwire has failed to engage
    Green LED = tripwire has finished initialising, system is ready for use
    [Laser_Tripwire.ino]
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2020-03-25 Efficiency improvements
    Adjusted order that tripwire testing occurs to require turning off/on laser only once
2020-03-25 Pin allocation changes
    Changed pin numbers to eliminate laser flickering due to being on pin 13, and to condense RGB pins together
2020-04-17 File created
    Added solid cylinder
    [Model.dwg]
2020-04-17 Corrected size of cylinder, hollowed centre
    [Model.dwg]
2020-04-17 Created insert hole at top of model
    [Model.dwg]
2020-04-17 Added hole for laser module
    [Model.dwg]
2020-04-17 Added hole for LDR sensor
    [Model.dwg]
2020-04-17 Added bottom funnel with drain hole
    [Model.dwg]
2020-04-17 Added peg model
    [Model.dwg]
2020-04-18 Added water jet holes
    [Model.dwg]
2020-04-18 Added water level sensor mount
    [Model.dwg]
2020-04-18 Added removable top
    [Model.dwg]
2020-04-18 Added removable base
    [Model.dwg]
2020-04-18 Added mount for buttons
    [Model.dwg]
2020-04-18 Refined button box
    [Model.dwg]
2020-04-18 Added threading for solenoid valve
    [Model.dwg]
2020-04-18 Added watering rose
    [Model.dwg]
2020-04-18 Added layers
    [Model.dwg]
2020-04-19 Added interlock to base
    [Model.dwg]
2020-04-19 Added interlock to solenoid valve components
    [Model.dwg]
2020-04-19 Removed old button box
    [Model.dwg]
2020-04-19 Added ring to prevent water egress through valve threading
    [Model.dwg]
2020-04-19 Increased size of water level sensor screw holes
    [Model.dwg]
2020-04-20 Removed cut-out for solenoid valve contacts
    Arduino/battery/button box WIP, will connect to main body through single connector
    [Model.dwg]
2020-04-20 Laid out electronics enclosure, WIP
    [Model.dwg]
2020-04-21 Reverted change to water level sensor holes
    Electronics enclosure WIP
    [Model.dwg]
2020-04-21 Increased size of water level sensor holes for M3
    M3 screws, diameter 3.2mm
    [Model.dwg]
2020-04-21 Completed electronics enclosure
    [Model.dwg]
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2020-04-21 Improved visual balance of arrangement
    Increased spacing between indicator and buttons, shifted buttons right
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2020-04-21 Redesigned label plate
2020-04-21 Moved modelling files into dedicated folder
    [Model.dwg]
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2020-04-22 Removed interlock for second valve component
    Would have been unable to thread valve into fitting while interlocked
    [Model.dwg]
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2020-04-27 Added reverse bias schottky diodes in solenoid circuit
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2020-04-28 Added wire routing hole for draining solenoid valve
    [Model.dwg]
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2020-04-28 Reversed solenoid polarity
    Pin 2 was connected to Vcc, pin 1 to GND
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2020-04-28 Renamed 3D model
    [Automatic Peg Cleaner.dwg]
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2020-04-28 Changed drainGate pin assignment
    Moved to D8 to allow for sufficient spacing between resistors on PCB
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2020-04-28 Moved jet solenoid valve FET switch circuit
    Moved to accomodate button control traces, trying to prevent overlap
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2020-04-28 Added battery GND traces to 'BATTERY' design rule
    BATTERY is old Vcc
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2020-04-28 Moved Q4 - R9 drainGate trace below RGB indicator connector
    Previously blocking greenPin and redPin from their digital pins above
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2020-04-28 Re-routed laser diode GND
    Moved to top layer to minimise total conflict with input pins
2020-04-28 Moved R1 battery GND trace to top layer
    Minimise total conflict with input pins
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2020-04-28 Rerouted lower battery GND connections
    Created a 'channel' on the bottom layer to route input pins through
2020-04-28 Swapped pin assignments for waterPin and ldrPin to avoid trace crossover
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2020-05-01 Testing power switch circuit using single NMOS
    Apparent voltage leak between Vin (always connected) and powerGate, which is engaging the source-drain channel and connecting the Arduino to GND
2020-05-01 Testing power switch circuit with relay mockup
    Relay is impractical for final implementation due to power consumption considerations alonside space restrictions, however is useful to demonstrate working circuit as its signal and switching connections are seperate, allowing me to switch Vin with GND always connected
    Note the fast engaging speed of the Arduino with bootloader removed, however is still not quick enough for very short pulses (therefore capacitor)
2020-05-02 Removed vias
    Reducing number of rivets required with Voltera printing, as each rivet is a potential error point
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2020-05-04 Completed layout
    Jet MOSFET cannot go below RGB indicator as traces would need to go through header pins
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2020-05-04 Routed laser diode
    Adjusted routing of solenoid VCC traces to accomodate laser diode traces
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2020-05-14 Testing analogRead values with water level sensor
    Note the residual reading of ~240 after being removed from the bowl as there is water stuck to the sensor
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2020-05-14 Testing MOSFET power circuit as per circuit diagram
    Arduino bootloader still installed, therefore short button presses still aren't long enough even with capacitor, LED is displaying powerGate state
2020-05-14 Testing MOSFET circuit without bootloader
    Near instantaneous presses still allow Arduino to boot and write powerGate HIGH due to capacitor
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2020-05-19 Corrected width of jet solenoid valve GND trace
2020-05-19 Fixed water level sensor mount
    Wasn't properly extruded, was previously an internal cavity in the sidewall rather than an inset mount
    [Automatic Peg Cleaner.dwg]
2020-05-19 Replaced enclosure connector mount to Digi-Key component
    [Automatic Peg Cleaner.dwg]
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2020-05-20 Corrected template for interlock
    Added 1mm tolerance to plates, 0.5mm tolerance to edges
    [Automatic Peg Cleaner.dwg]
2020-05-20 Fixed interlock on lid
    [Automatic Peg Cleaner.dwg]
2020-05-20 Fixed top interlock on body
    [Automatic Peg Cleaner.dwg]
2020-05-20 Fixed bottom interlock on body
    [Automatic Peg Cleaner.dwg]
2020-05-20 Fixed interlocking brace
    [Automatic Peg Cleaner.dwg]
2020-05-20 Added tolerance to alignment beams in base
    [Automatic Peg Cleaner.dwg]
2020-05-20 Added tolerance to locking pegs in lid of electronics enclosure
    [Automatic Peg Cleaner.dwg]
2020-05-20 Added 0.5mm tolerance to inset acrylic labels in enclosure lid
    [Automatic Peg Cleaner.dwg]
2020-05-20 Test print issues due to lack of tolerance in designs
    Likely due to additive print process, alongside non-instantaneous cooling leading to warping and expansion
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2020-05-22 Reduced tolerances in interlock
    0.5mm between plates, 0.25mm between edges
    [Automatic Peg Cleaner.dwg]
2020-05-23 Reduced acrylic inset vertical tolerance to 0.25mm
    [Automatic Peg Cleaner.dwg]
2020-05-23 Reduced tolerance on lid interlock
    [Automatic Peg Cleaner.dwg]
2020-05-23 Reduced tolerance on top body interlock
    [Automatic Peg Cleaner.dwg]
2020-05-23 Reduced tolerance on bottom body interlock
    [Automatic Peg Cleaner.dwg]
2020-05-23 Reduced tolerance in interlocking brace
    [Automatic Peg Cleaner.dwg]
2020-05-23 Reduced tolerance on base alignment beams
    [Automatic Peg Cleaner.dwg]
2020-05-23 Reduced tolerance on enclosure lid pegs
    [Automatic Peg Cleaner.dwg]
2020-05-23 Added interlocking trench to enclosure lid/body
    [Automatic Peg Cleaner.dwg]
2020-05-23 Reduced tolerance in base diameter to 0.25mm
    Radius = 50.125mm
    [Automatic Peg Cleaner.dwg]
2020-05-23 Testing various taper angles for optimal fit
    Right to left: -1, -0.75, edge of socket, -0.7, -0.65, -0.5, 0 degrees
2020-05-24 Fixed calculaton to find triggerAt
    Refer to https://www.desmos.com/calculator/1yy5bewkri - previous algorithm only worked if disarmedValue was roughly half of maximumValue
    [Laser_Tripwire.ino]
2020-05-25 Removed 1.25mm from bottom of water level sensor mount following testing
    [Automatic Peg Cleaner.dwg]
2020-05-25 Removed 0.125mm on all sides of connector mount, added panel mount ears lock
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2020-05-26 Seperated bottom rose to improve printing quality
    Would have been unnecessarily difficult to remove support structures, added interlocking to print in two parts
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2020-05-26 Added 0.5mm total tolerance to interlock for laser diode and LDR
    0.25mm offset in all directions
2020-05-26 Improved clearances and tolerances in connector mount
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2020-05-27 Fixed Arduino mounting hole location
    [Automatic Peg Cleaner.dwg]
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2020-06-05 Added voltage divider for reading battery voltage
    Changed analogue pin assignments to accomodate trace routing
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2020-06-08 Testing battery state code
    Using 5V, 3.3V and 20k/6.8k voltage divider to test with different voltage levels
2020-06-08 Successful result from test of friction fitting 3D model using tapered insert
    -0.65 degrees (test model III)
2020-06-08 Connector mount needs more depth, not enough space for panel mount ear to latch
2020-06-08 Changed support z distance and support density
    Changed z distance from 0.1mm to 0.2mm and support density from 20% to 10%, supports are now significantly easier to remove
2020-06-08 Insufficient clearance on top edges requiring filing to fit connector
2020-06-08 Not enough clearance on bottom requiring removal of around 1.5mm of material
2020-06-08 Significant improvement in tolerances, acceptable quality for final print
2020-06-08 Rose model requires re-design, internal support material is too difficult to remove and results in a less than ideal surface
2020-06-08 Significant improvement in mount for water level sensor, alignment is acceptable for final print
2020-06-08 Connector mount model finalised, panel mount ears interlock correctly and fit well
2020-06-08 Error in 3D model for Arduino mount, one mounting hole is incorrectly spaced
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2020-07-01 Adjusted tolerances in base to streamline fit
    [Automatic Peg Cleaner.dwg]
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2020-09-08 Homogenised thickness of solenoid brace
    [Automatic Peg Cleaner.dwg]
2020-09-09 Added holes in box for hose fittings
    [Automatic Peg Cleaner.dwg]
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2020-09-21 Changed while statement to if statement for laser tripwire; reset drain/indicator after water danger is addressed
    [Peg Cleaner.ino]
2020-09-21 Turn Arduino off if error occurs
    [Peg Cleaner.ino]
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2020-09-21 Added reset lastAction timer to drain button; removed drainDelay as it is 'blocking' code
    [Peg Cleaner.ino]
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2020-09-21 Fixed time out functionality
    [Peg Cleaner.ino]
2020-09-21 Pause before turning off if error occurs
    [Peg Cleaner.ino]
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2020-09-21 Changed behaviour if tripwire malfunctions
    Doesn't turn off; just keeps blinking alert
    [Peg Cleaner.ino]
2020-09-21 Fixed batteryValue analogRead by converting value into voltage value
    [Peg Cleaner.ino]
2020-09-21 Fixed indicatorAlert > indicatorControl
    [Peg Cleaner.ino]
2020-09-21 Fixed else if after while statement
    [Peg Cleaner.ino]
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2020-09-22 Fixed indicatorAlert()
    Actually blinks; before the LEDs wouldn't be turned off
    [Peg Cleaner.ino]
2020-09-22 Fixed terminateNotify
    Previously, LEDs would blink then shut down regardless of user input, now there is a 10 second (15 seconds in advance, 5 seconds taken by the for loop) window to refresh
    [Peg Cleaner.ino]
2020-09-23 Moved analogRead and digitalRead statements into respective functions checkTurnOff() would not work previously while stuck in tripwireCheck() as offInput would not update
    [Peg Cleaner.ino]
2020-09-23 Fixed analogRead(ldrValue) to analogRead(ldrPin)
    [Peg Cleaner.ino]
2020-09-23 Swapped if/else statements in checkTurnOff() Would previously never run the else if code; as if was always satisfied
    [Peg Cleaner.ino]
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2020-09-24 pinState would reset to HIGH each repetition
    Therefore would never turn off
    [Peg Cleaner.ino]
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2020-09-24 If LDR is disconnected for one iteration of the for loop, skip completely
    Previously, LDR could be connected half-way through a loop
    [Peg Cleaner.ino]
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2020-09-28 As for loop continues if ldrPin is 0, disarmedValue should never be 0, and so we can now expand the scope to not only if LDR is disconnected, but if tripwire fails to arm
    [Peg Cleaner.ino]
2020-09-28 Added Serial print statements to debug
    Functions correctly if LDR disconnected still, but tripwire arm doesn't
    [Peg Cleaner.ino]
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2020-09-28 Simple fix: ldrValue was not being updated in the while loop :/
    [Peg Cleaner.ino]
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2020-09-28 Testing adding a fluctuation trigger, i.e. if testTotal changes outside of a tolerance for loop will break
    [Peg Cleaner.ino]
2020-09-28 Fixed dividing by 0 error
    [Peg Cleaner.ino]
2020-09-28 Break if fluctuation is outside tolerance
    Can remove ldr disconnected break statement, as it would be covered by the fluctuation check
    [Peg Cleaner.ino]
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2020-10-22 Broken snap-fit inserts
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2020-10-22 Shield bottom layer clearance with grounded USB connector
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2022-05-12 chore: :bento: upload schematic and pcb images
2022-05-13 chore: :bento: upload schematic as `.svg`
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2022-08-15 docs: :memo: add assessment submissions
    [BOM.xlsx]
